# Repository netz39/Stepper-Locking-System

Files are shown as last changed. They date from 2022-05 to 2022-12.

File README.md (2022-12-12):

# Stepper Locking System

Steering the key/door knob with the might of stepper motors.
See the [Wiki](https://wiki.netz39.de/projects:2022:stepper_locking_system) (german) for more details and an overview.

This is forked from https://github.com/sprenger120/StepperServo.

## Firmware
The firmware written in C++ is [here](https://github.com/netz39/Stepper-Locking-System_firmware).

## Requirements for v1.0

* control stepper motor with Trinamic IC
* hall encoder connection to get current motor state
* read motor temperature
* CAN peripherie (dedicated PCB)
* power rails are secured by two fuses, with reverse polarity/overvoltage protection
* drive syncronous addressable LEDs
* get states from door and lock
* connection to two buttons to open/close door
* switch on/off Nerdstern (outdoor lamp)

## Known issues in v1.0
* Mosfet Q1 has wrong connections for choosen part. Gate and Source are swapped.
    * can be solved by simply solder the part upside down
* the LQFP32 package of STM32G0B1KE doesn't support HSE connection
    * the internal HSI is used

## Pictures (v1.0)

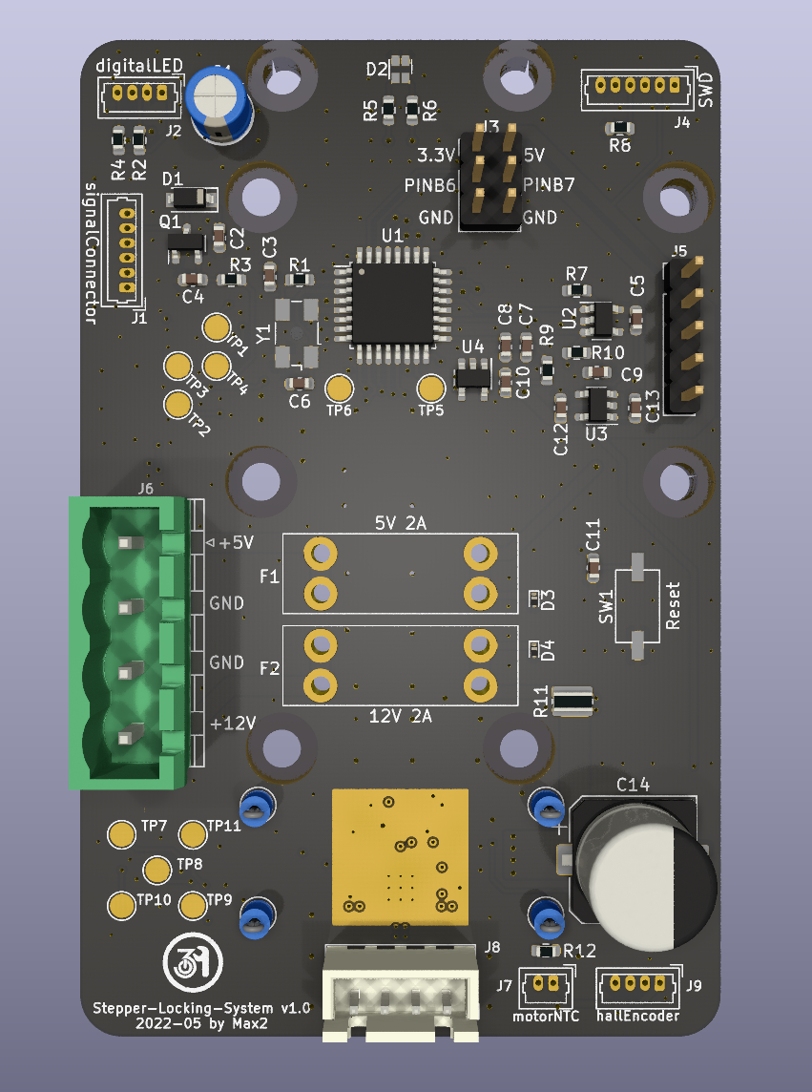
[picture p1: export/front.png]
pcb front front view


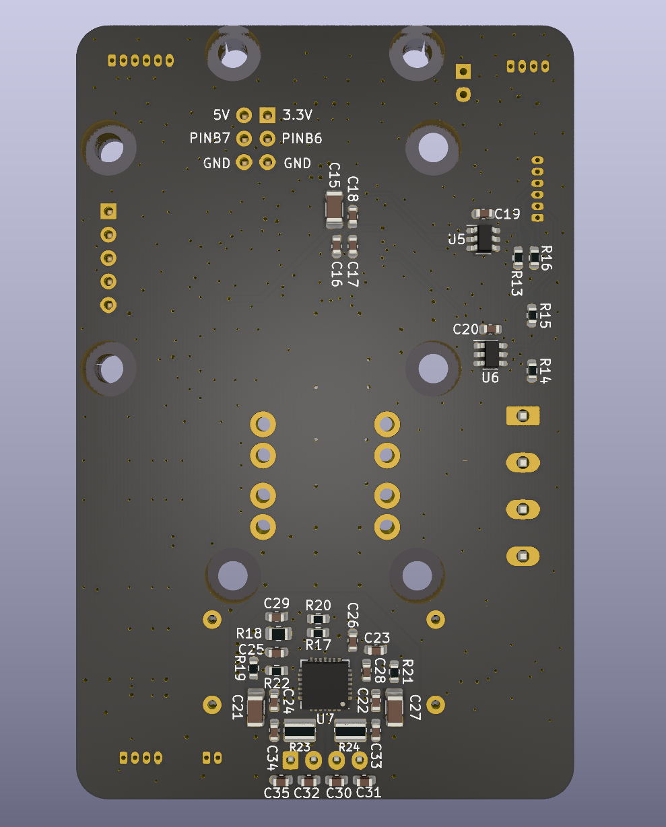
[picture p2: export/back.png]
pcb back back view


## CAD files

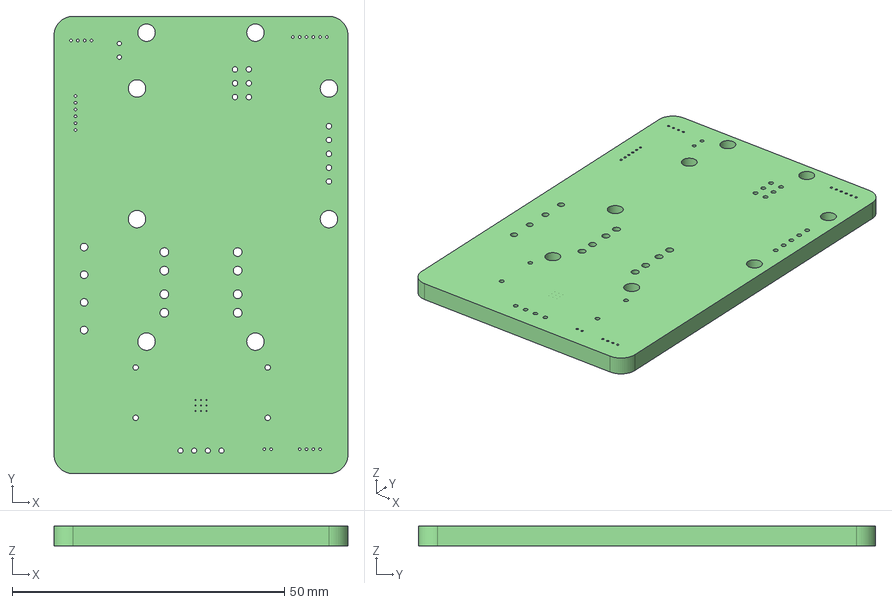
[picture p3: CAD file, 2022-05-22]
export/StepperLockingSystem.step
54.0 x 84.0 x 3.66 mm

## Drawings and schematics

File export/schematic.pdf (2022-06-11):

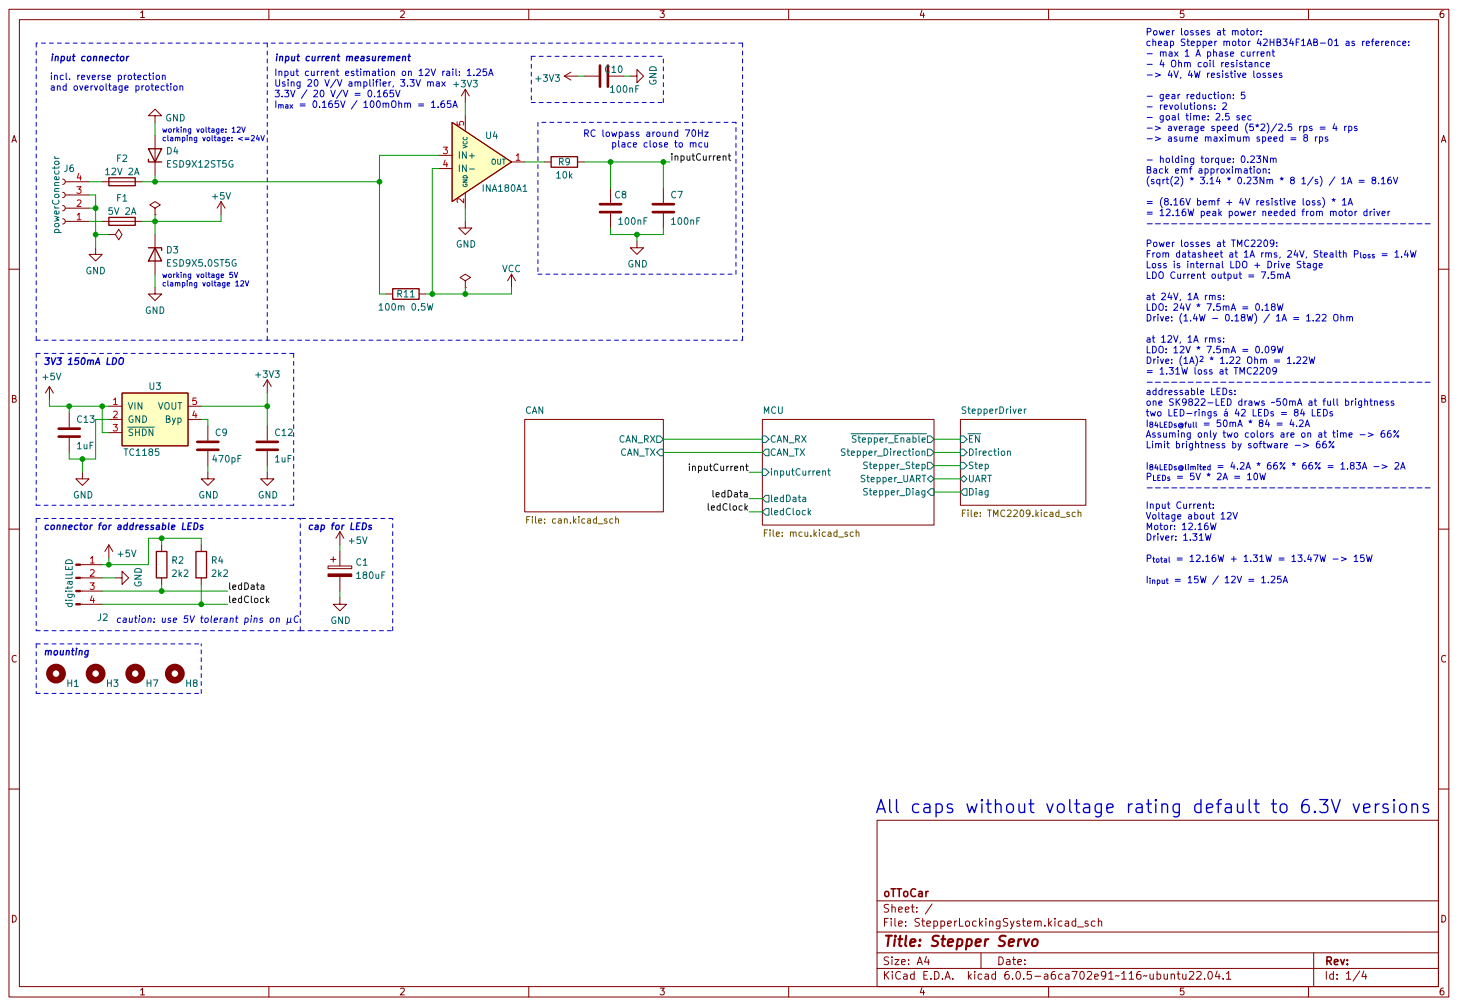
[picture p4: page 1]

- max 1 A phase current - 4 Ohm coil resistance

input current measurement 3V3 150mA LDO
incl. reverse protection
and overvoltage protection

Input current estimation on 12V rail: 1.25A
Using 20 V/V amplifier, 3.3V max 3.3V / 20 V/V = 0.165V

- gear reduction: 5
- revolutions: 2
- goal time: 2.5 sec
-> average speed (5*2)/2.5 rps = 4 rps
-> asume maximum speed = 8 rps

= (8.16V bemf + 4V resistive loss) * 1A
= 12.16W peak power needed from motor driver

----------------------------------- Power losses at TMC2209: From datasheet at 1A rms, 24V, Stealth P_{loss} = 1.4W

Loss is internal LDO + Drive Stage
LDO Current output = 7.5mA

Drive: (1A)^{2} * 1.22 Ohm = 1.22W
= 1.31W loss at TMC2209
addressable LEDs: one SK9822-LED draws ~50mA at full brightness

----------------------------------- All caps without voltage rating default to 6.3V versions
ledClock MCU

File: StepperLockingSystem.kicad_sch Sheet: / oTToCar CAN_RX CAN_TX CAN

I_{84LEDs@full} = 50mA * 84 = 4.2A
Assuming only two colors are on at time -> 66%
Limit brightness by software -> 66%

connector for addressable LEDs

Id: 1/4 Title: Stepper Servo

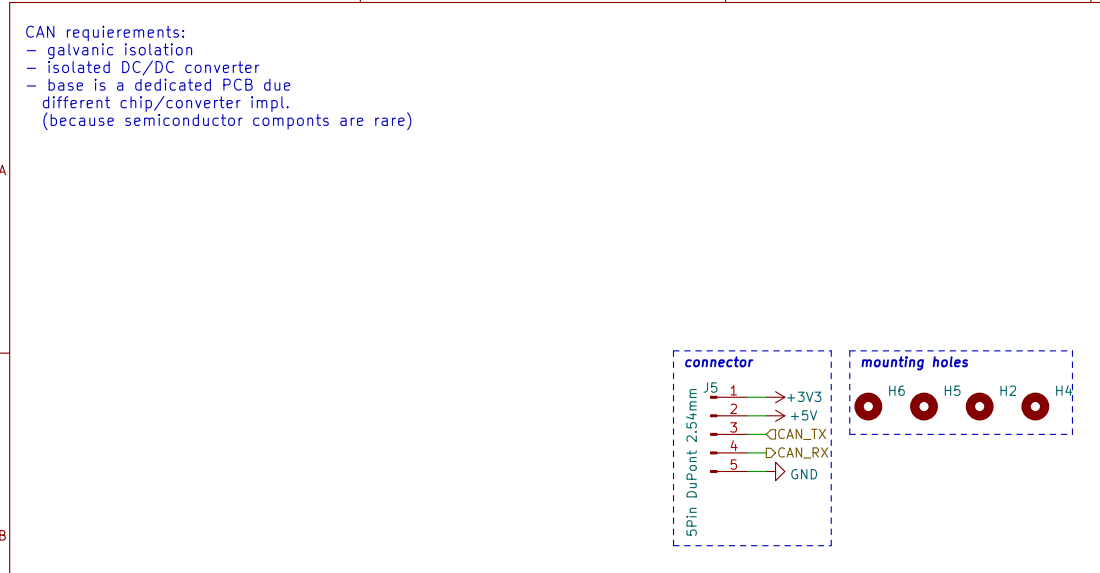
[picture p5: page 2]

CAN requierements:
- galvanic isolation
- isolated DC/DC converter
- base is a dedicated PCB due
different chip/converter impl.
(because semiconductor componts are rare)

File: can.kicad_sch Sheet: /CAN/
Id: 4/4 Title:

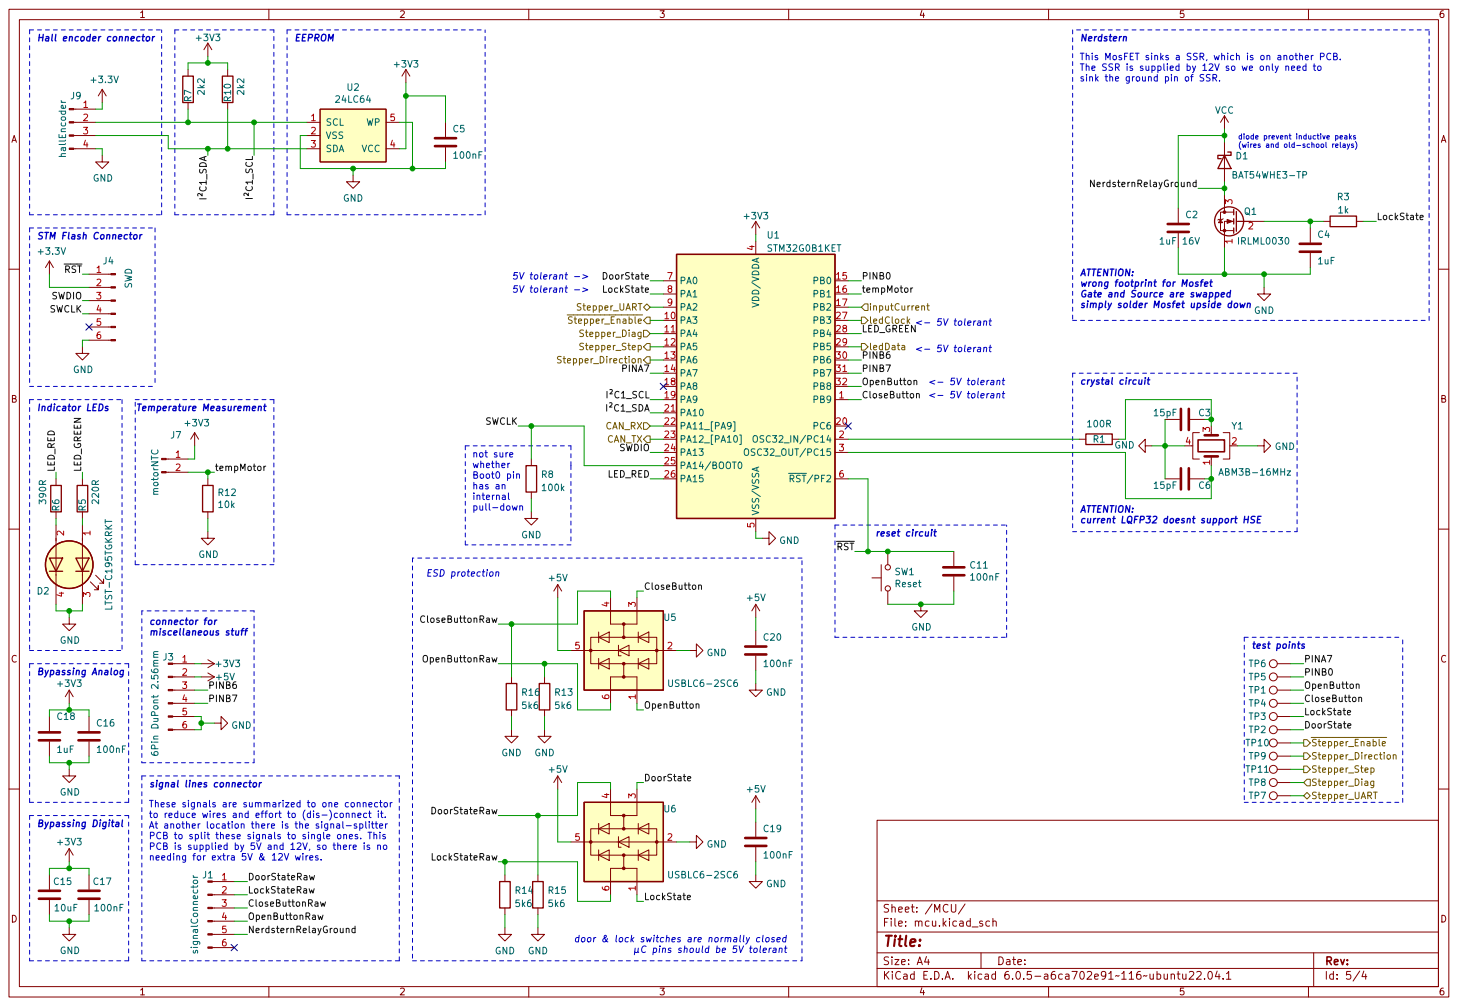
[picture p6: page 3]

Nerdstern
This MosFET sinks a SSR, which is on another PCB. The SSR is supplied by 12V so we only need to

(wires and old-school relays) not sure whether Boot0 pin

Gate and Source are swapped
simply solder Mosfet upside down

LockState CloseButton PINA7 PINA7 SWCLK DoorStateRaw

to reduce wires and effort to (dis-)connect it.
At another location there is the signal-splitter
PCB to split these signals to single ones. This
PCB is supplied by 5V and 12V, so there is no
needing for extra 5V & 12V wires.

File: mcu.kicad_sch Sheet: /MCU/
Id: 5/4 Title:

door & lock switches are normally closed

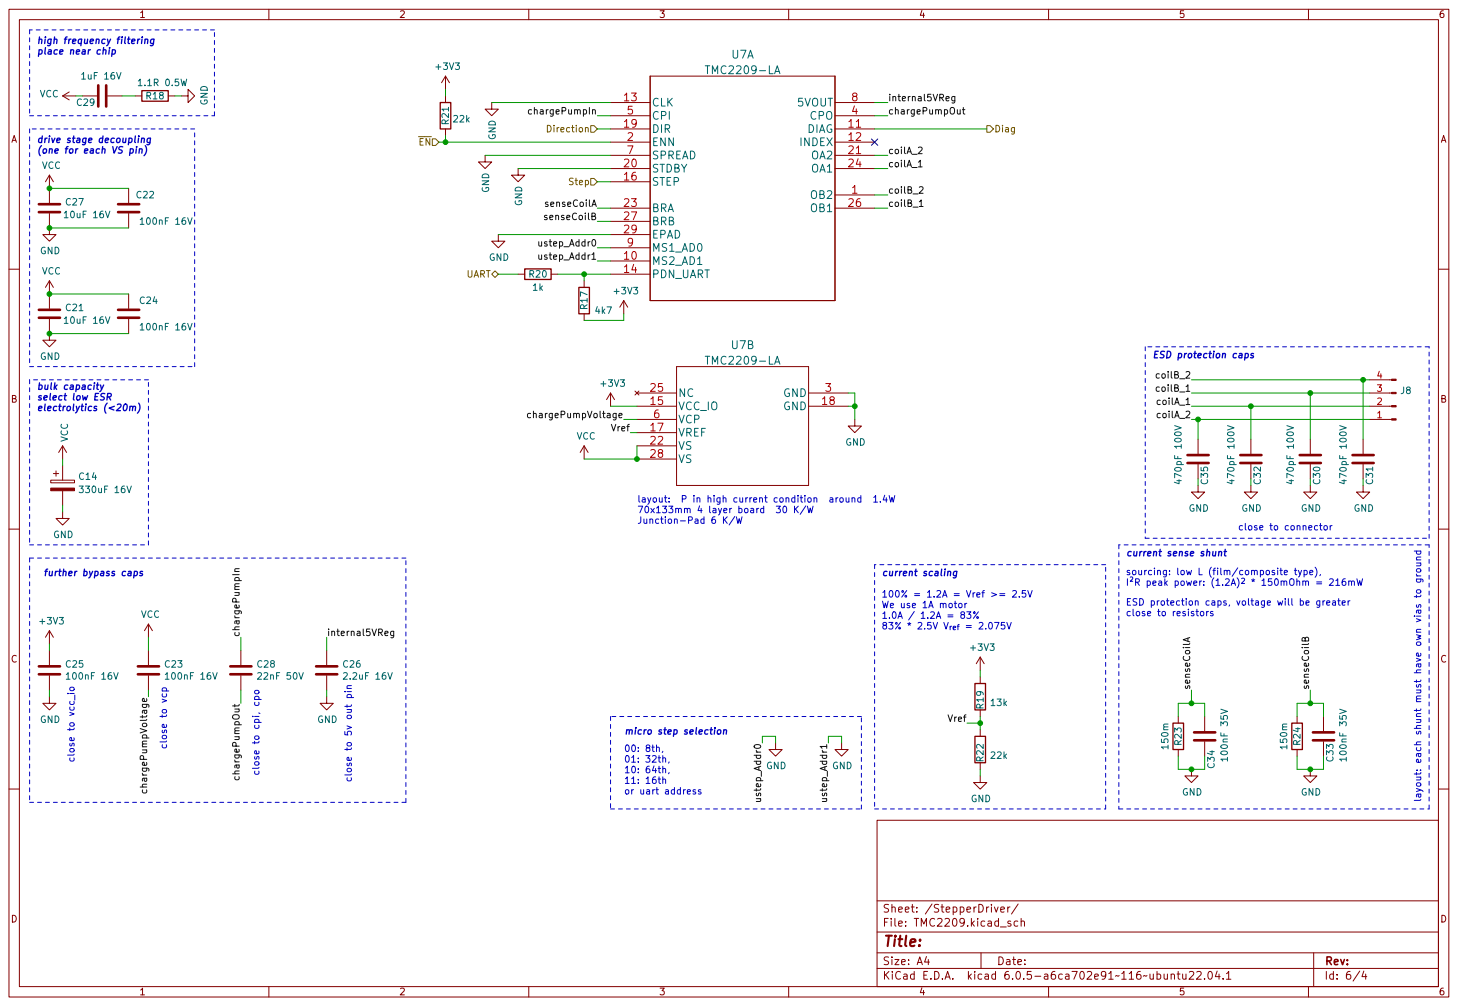
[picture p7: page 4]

Sheet: /StepperDriver/ GND VCC GND

layout: P in high current condition around 1.4W
70x133mm 4 layer board 30 K/W
Junction-Pad 6 K/W

current sense shunt close to 5v out pin

further bypass caps | 22nF 50V C23

current scaling 83% * 2.5V V_{ref} = 2.075V

sourcing: low L (film/composite type),

Vref 100% = 1.2A = Vref >= 2.5V We use 1A motor 1.0A / 1.2A = 83%

ESD protection caps, voltage will be greater close to resistors

or uart address micro step selection

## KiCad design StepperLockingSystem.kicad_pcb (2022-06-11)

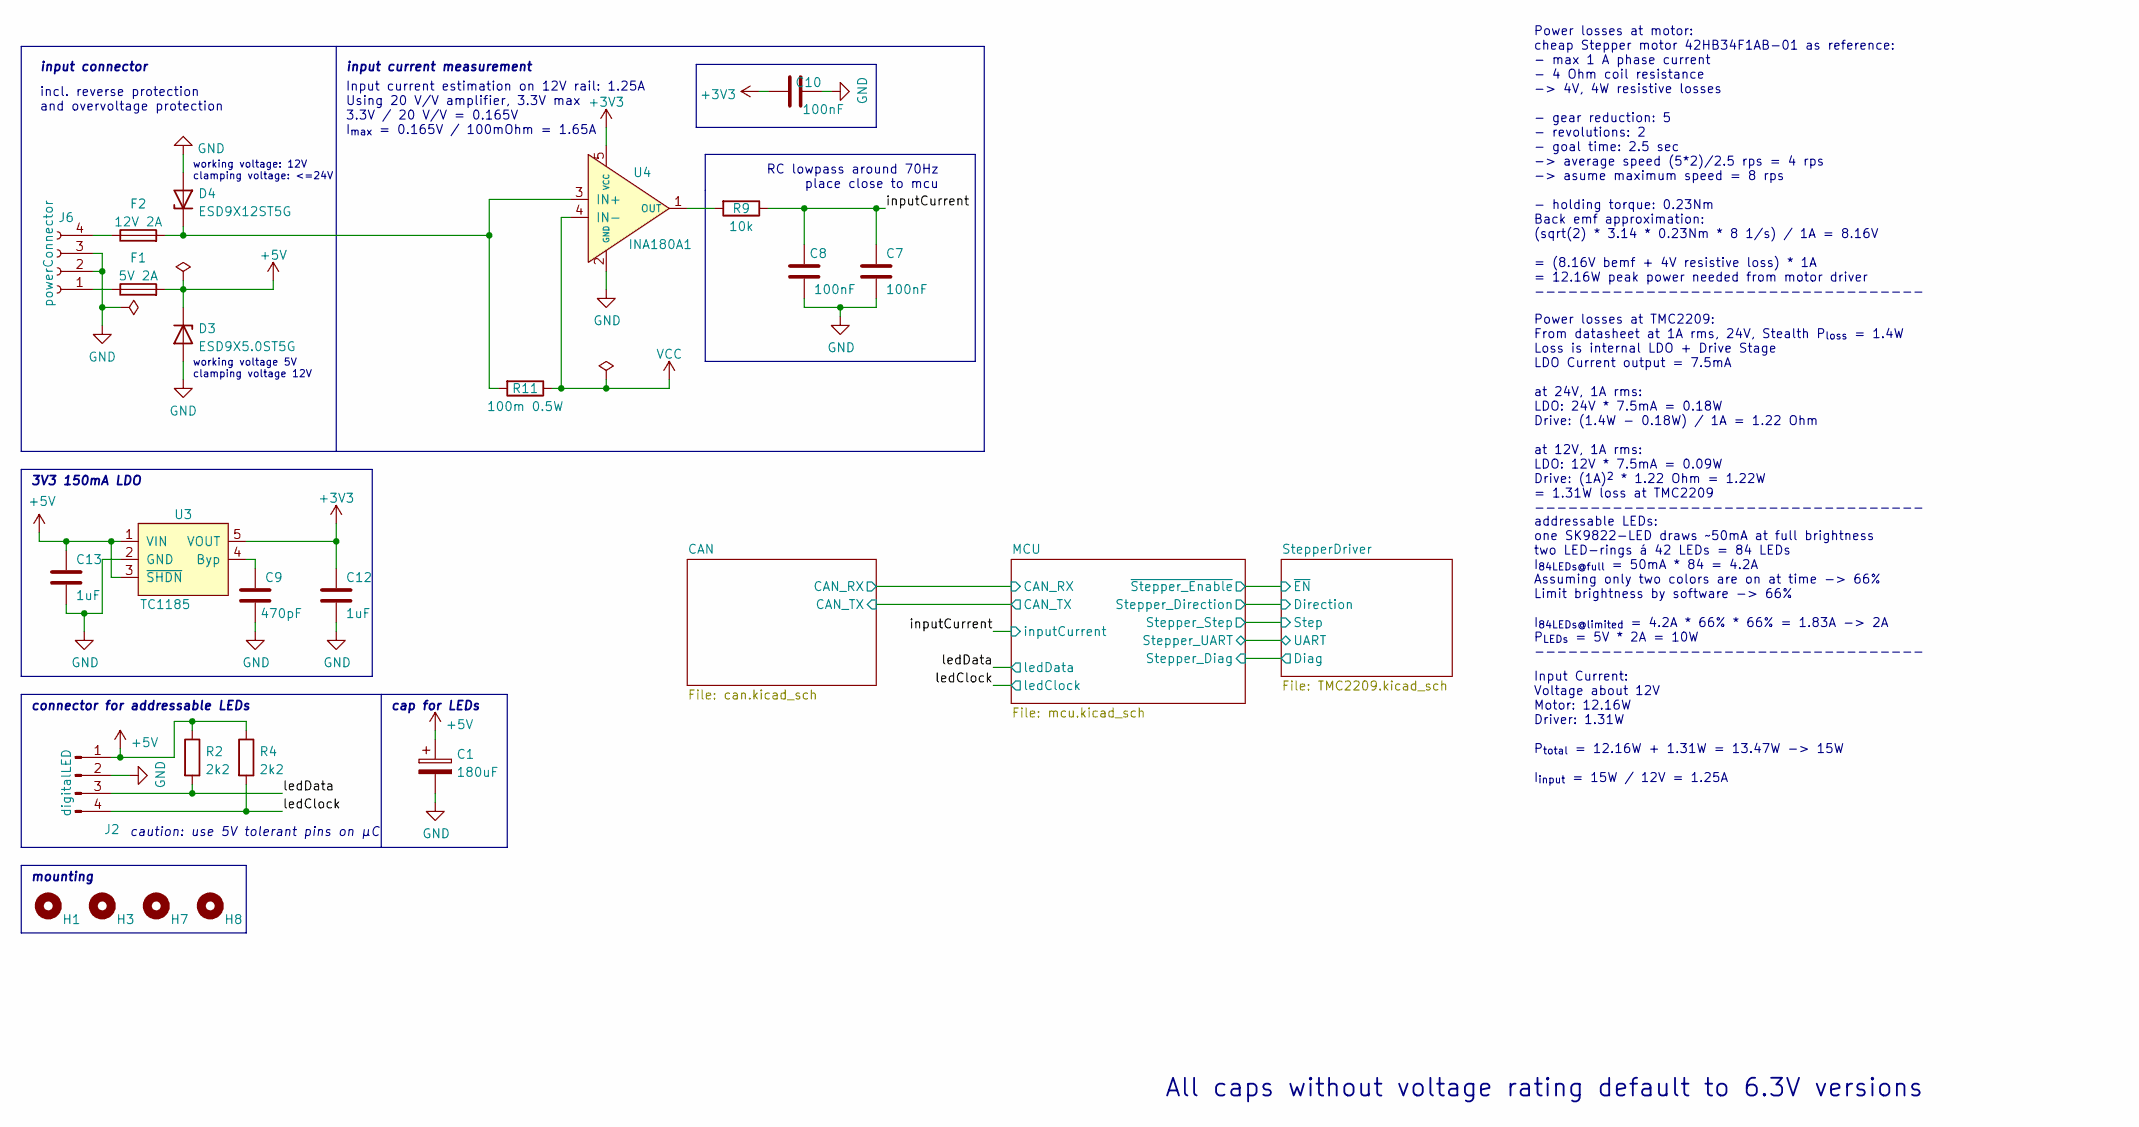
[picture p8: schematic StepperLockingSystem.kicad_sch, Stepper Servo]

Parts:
C1: 180uF; CP_Radial_D5.0mm_P2.50mm
C7, C8, C10: 100nF; C_0603_1608Metric
C9: 470pF; C_0603_1608Metric
C12, C13: 1uF; C_0603_1608Metric
D3: ESD9X5.0ST5G; D_SOD-923
D4: ESD9X12ST5G; D_SOD-923
F1: 5V 2A; KEYSTONE-FUSE-3557-2
F2: 12V 2A; KEYSTONE-FUSE-3557-2
H1, H3, H7, H8: MountingHole_Pad; MountingHole_3.2mm_M3_ISO7380_Keepout
J2: digitalLED; Molex_PicoBlade_53047-0410_1x04_P1.25mm_Vertical
J6: powerConnector; PhoenixContact_MSTBVA_2,5_4-G-5,08_1x04_P5.08mm_Vertical
R2, R4: 2k2; R_0603_1608Metric
R9: 10k; R_0603_1608Metric
R11: 100m 0.5W; R_0612_1632Metric
U3: TC1185; SOT-23-5
U4: INA180A1; SOT-23-5

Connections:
+5V: C1.1, C13.1, D3.1 (K), F1.2, J2.1, R2.1, R4.1, U3.1 (VIN), U3.3 (~SHDN); also elsewhere on the board
/inputCurrent: C7.1, C8.1, R9.1; also elsewhere on the board
/ledClock: J2.4, R4.2; also elsewhere on the board
/ledData: J2.3, R2.2; also elsewhere on the board
GND: C1.2, C7.2, C8.2, C9.2, C10.2, C12.2, C13.2, D3.2 (A), D4.2 (A), J2.2, J6.2, J6.3, U3.2 (GND), U4.2 (GND); also elsewhere on the board
unnamed: C9.1, U3.4 (Byp)
unnamed: D4.1 (K), F2.2, R11.2, U4.3 (IN+)
unnamed: F1.1, J6.1
unnamed: F2.1, J6.4
unnamed: R9.2, U4.1 (OUT)
VCC: R11.1, U4.4 (IN-); also elsewhere on the board

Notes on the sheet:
All caps without voltage rating default to 6.3V versions
caution: use 5V tolerant pins on µC
working voltage: 12V clamping voltage: <=24V
Input current estimation on 12V rail: 1.25A Using 20 V/V amplifier, 3.3V max 3.3V / 20 V/V = 0.165V I_{max} = 0.165V / 100mOhm = 1.65A
Power losses at TMC2209: From datasheet at 1A rms, 24V, Stealth P_{loss} = 1.4W Loss is internal LDO + Drive Stage LDO Current output = 7.5mA at 24V, 1A rms: LDO: 24V * 7.5mA = 0.18W Drive: (1.4W - 0.18W) / 1A = 1.22 Ohm at 12V, 1A rms: LDO: 12V * 7.5mA = 0.09W Drive: (1A)^{2} * 1.22 Ohm = 1.22W = 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
RC lowpass around 70Hz place close to mcu
working voltage 5V clamping voltage 12V
input connector
addressable LEDs: one SK9822-LED draws ~50mA at full brightness two LED-rings á 42 LEDs = 84 LEDs I_{84LEDs@full} = 50mA * 84 = 4.2A Assuming only two colors are on at time -> 66% Limit brightness by software -> 66% I_{84LEDs@limited} = 4.2A * 66% * 66% = 1.83A -> 2A P_{LEDs} = 5V * 2A = 10W ------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
3V3 150mA LDO
connector for addressable LEDs
input current measurement
cap for LEDs
incl. reverse protection and overvoltage protection
mounting
Input Current: Voltage about 12V Motor: 12.16W Driver: 1.31W P_{total} = 12.16W + 1.31W = 13.47W -> 15W I_{input} = 15W / 12V = 1.25A
Power losses at motor: cheap Stepper motor 42HB34F1AB-01 as reference: - max 1 A phase current - 4 Ohm coil resistance -> 4V, 4W resistive losses - gear reduction: 5 - revolutions: 2 - goal time: 2.5 sec -> average speed (5*2)/2.5 rps = 4 rps -> asume maximum speed = 8 rps - holding torque: 0.23Nm 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

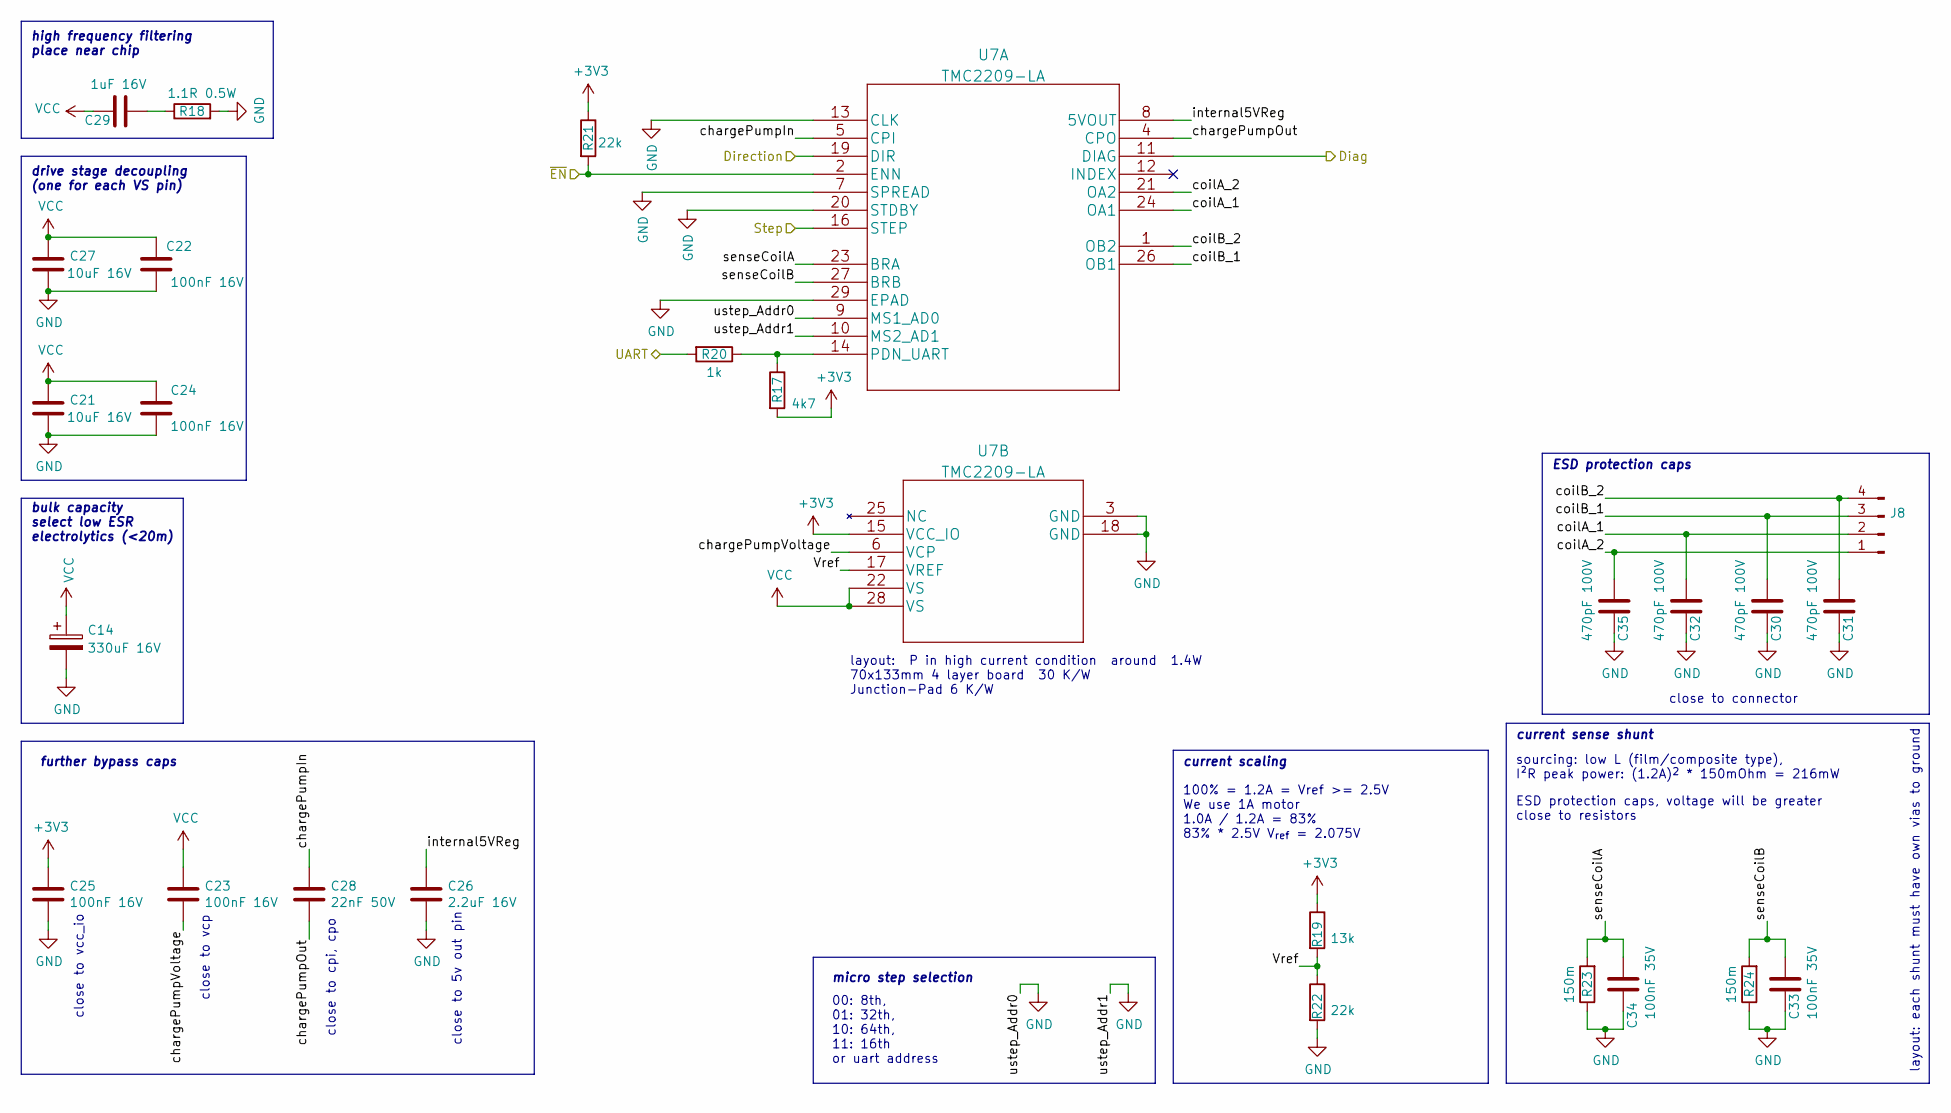
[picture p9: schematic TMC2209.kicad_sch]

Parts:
C14: 330uF 16V; CP_Elec_10x10.5
C21, C27: 10uF 16V; C_1206_3216Metric
C22, C23, C24, C25: 100nF 16V; C_0603_1608Metric
C26: 2.2uF 16V; C_0603_1608Metric
C28: 22nF 50V; C_0603_1608Metric
C29: 1uF 16V; C_0603_1608Metric
C30, C31, C32, C35: 470pF 100V; C_0603_1608Metric
C33, C34: 100nF 35V; C_0603_1608Metric
J8: Stepper; JST_XH_B4B-XH-A_1x04_P2.50mm_Vertical
R17: 4k7; R_0603_1608Metric
R18: 1.1R 0.5W; R_0805_2012Metric
R19: 13k; R_0603_1608Metric
R20: 1k; R_0603_1608Metric
R21, R22: 22k; R_0603_1608Metric
R23, R24: 150m; R_0612_1632Metric
U7: TMC2209-LA; QFN-28-1EP_5x5mm_P0.5mm_EP3.35x3.35mm_ThermalVias

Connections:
/MCU/Stepper_Diag: U7.11 (DIAG); also elsewhere on the board
/MCU/Stepper_Direction: U7.19 (DIR); also elsewhere on the board
/MCU/Stepper_Step: U7.16 (STEP); also elsewhere on the board
/MCU/Stepper_UART: R20.2; also elsewhere on the board
/MCU/~Stepper_Enable: R21.2, U7.2 (ENN); also elsewhere on the board
/StepperDriver/Vref: R19.2, R22.1, U7.17 (VREF)
/StepperDriver/chargePumpIn: C28.1, U7.5 (CPI)
/StepperDriver/chargePumpOut: C28.2, U7.4 (CPO)
/StepperDriver/chargePumpVoltage: C23.2, U7.6 (VCP)
/StepperDriver/coilA_1: C32.1, J8.2, U7.24 (OA1)
/StepperDriver/coilA_2: C35.1, J8.1, U7.21 (OA2)
/StepperDriver/coilB_1: C30.1, J8.3, U7.26 (OB1)
/StepperDriver/coilB_2: C31.1, J8.4, U7.1 (OB2)
/StepperDriver/internal5VReg: C26.1, U7.8 (5VOUT)
/StepperDriver/senseCoilA: C34.1, R23.2, U7.23 (BRA)
/StepperDriver/senseCoilB: C33.1, R24.2, U7.27 (BRB)
GND: C14.2, C21.2, C22.2, C24.2, C25.2, C26.2, C27.2, C30.2, C31.2, C32.2, C33.2, C34.2, C35.2, R18.2, R22.2, R23.1, R24.1, U7.3 (GND), U7.7 (SPREAD), U7.9 (MS1_AD0), U7.10 (MS2_AD1), U7.13 (CLK), U7.18 (GND), U7.20 (STDBY), U7.29 (EPAD); also elsewhere on the board
unnamed: C29.2, R18.1
unnamed: R17.1, R20.1, U7.14 (PDN_UART)
VCC: C14.1, C21.1, C22.1, C23.1, C24.1, C27.1, C29.1, U7.22 (VS), U7.28 (VS); also elsewhere on the board

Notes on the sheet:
layout: each shunt must have own vias to ground
100% = 1.2A = Vref >= 2.5V We use 1A motor 1.0A / 1.2A = 83% 83% * 2.5V V_{ref} = 2.075V
close to connector
close to vcc_io
bulk capacity select low ESR electrolytics (<20m)
drive stage decoupling (one for each VS pin)
current scaling
further bypass caps
micro step selection
ESD protection caps, voltage will be greater close to resistors
sourcing: low L (film/composite type), I²R peak power: (1.2A)^{2} * 150mOhm = 216mW
close to vcp
current sense shunt
close to cpi, cpo
00: 8th, 01: 32th, 10: 64th, 11: 16th or uart address
ESD protection caps
layout: P in high current condition around 1.4W 70x133mm 4 layer board 30 K/W Junction-Pad 6 K/W
high frequency filtering place near chip
close to 5v out pin

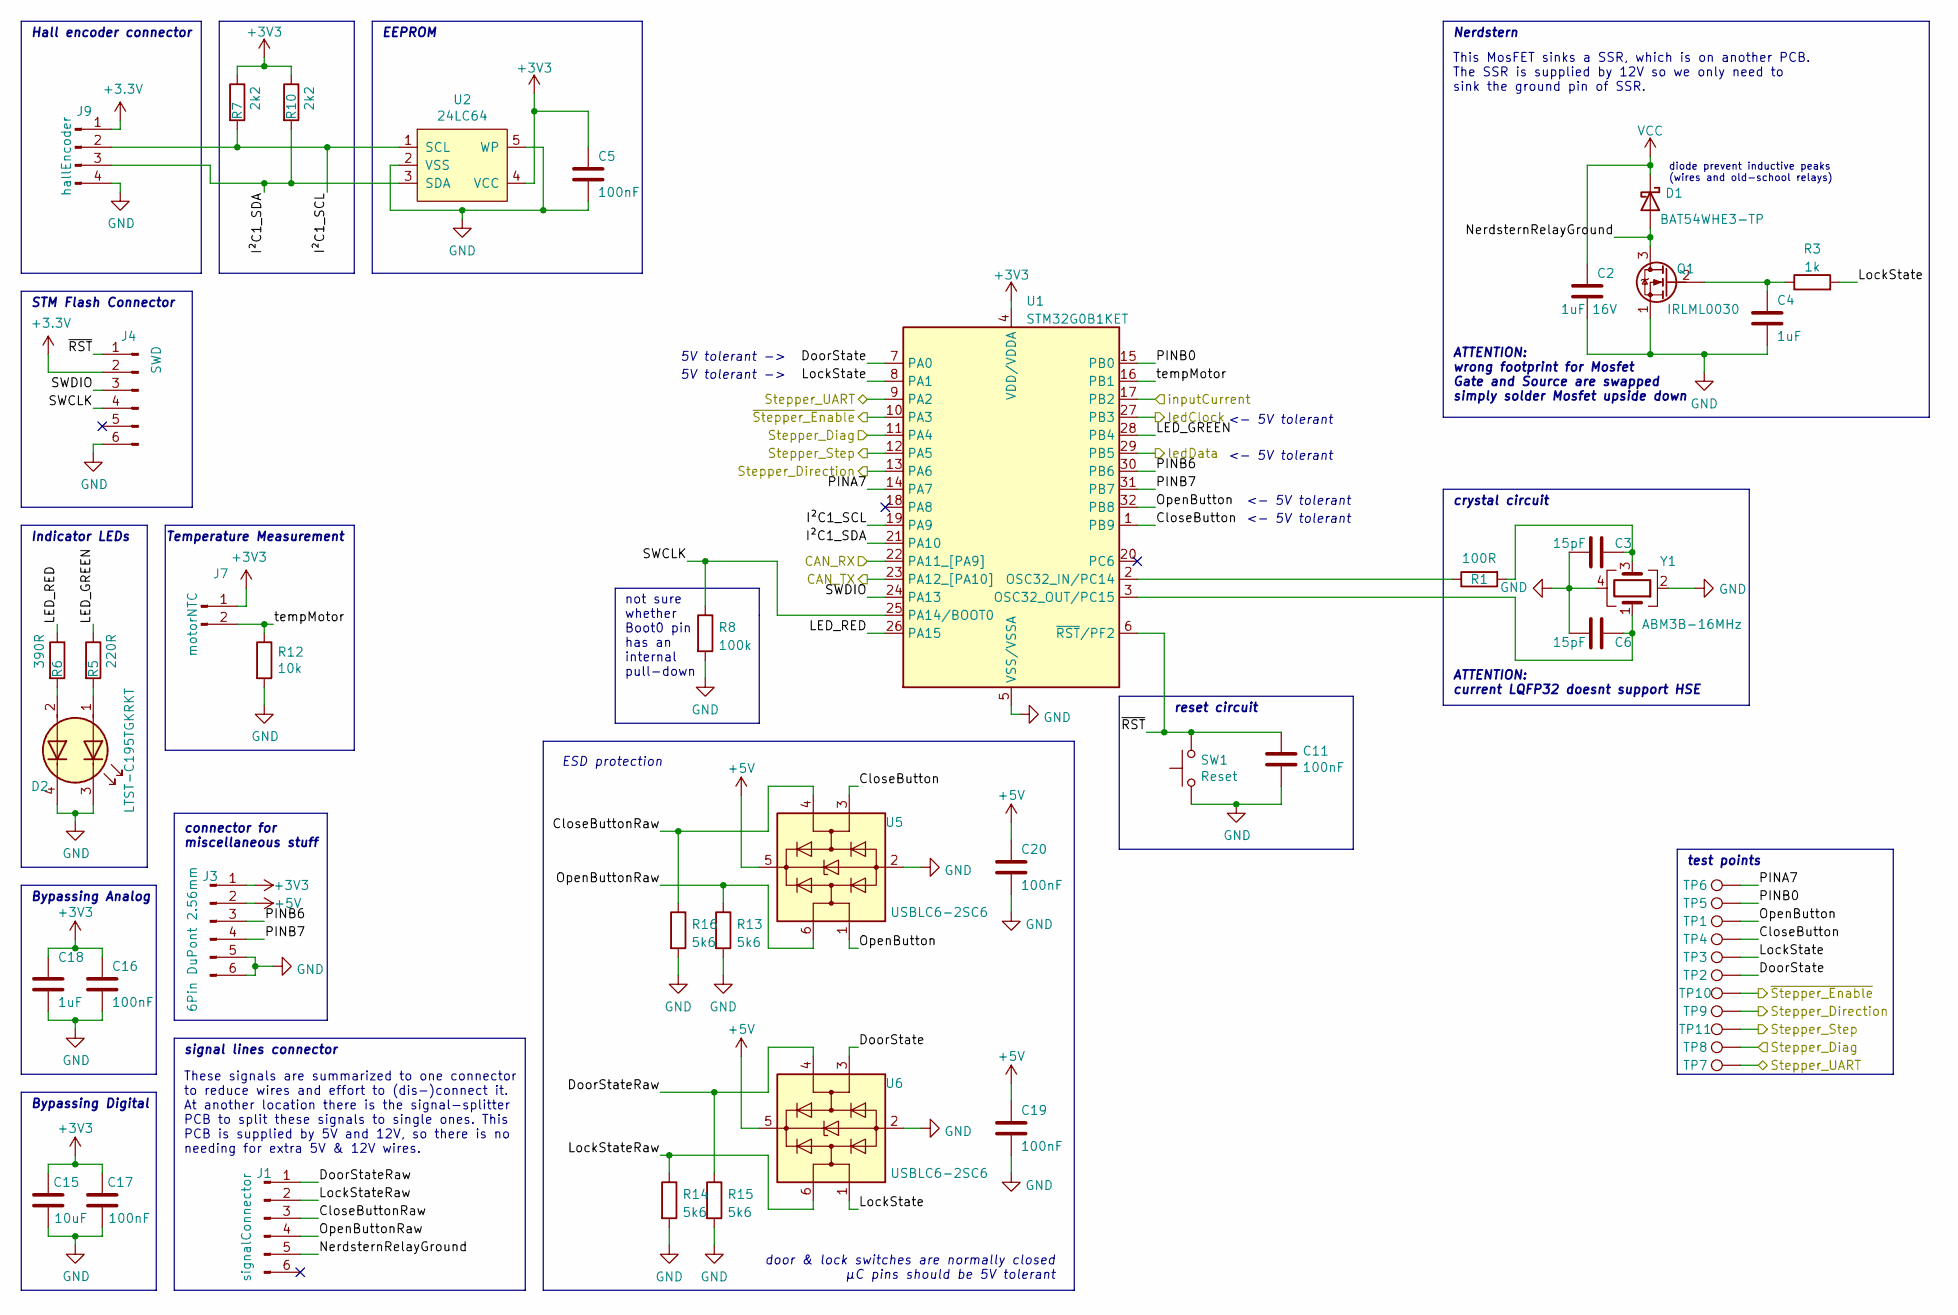
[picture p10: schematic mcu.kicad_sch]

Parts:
C2: 1uF 16V; C_0603_1608Metric
C3, C6: 15pF; C_0603_1608Metric
C4, C18: 1uF; C_0603_1608Metric
C5, C11, C16, C17, C19, C20: 100nF; C_0603_1608Metric
C15: 10uF; C_1206_3216Metric
D1: BAT54WHE3-TP; D_SOD-123
D2: LTST-C195TGKRKT; LED_LiteOn_LTST-C195TGKRKT
J1: signalConnector; Molex_PicoBlade_53047-0610_1x06_P1.25mm_Vertical
J3: 6Pin DuPont 2.56mm; PinHeader_2x03_P2.54mm_Vertical
J4: SWD; Molex_PicoBlade_53047-0610_1x06_P1.25mm_Vertical
J7: motorNTC; Molex_PicoBlade_53047-0210_1x02_P1.25mm_Vertical
J9: hallEncoder; Molex_PicoBlade_53047-0410_1x04_P1.25mm_Vertical
Q1: IRLML0030; SOT-23
R1: 100R; R_0603_1608Metric
R3: 1k; R_0603_1608Metric
R5: 220R; R_0603_1608Metric
R6: 390R; R_0603_1608Metric
R7, R10: 2k2; R_0603_1608Metric
R8: 100k; R_0603_1608Metric
R12: 10k; R_0603_1608Metric
R13, R14, R15, R16: 5k6; R_0603_1608Metric
SW1: Reset; PTS636_F-leads
TP1, TP2, TP3, TP4, TP5, TP6, TP7, TP8, TP9, TP10, TP11: TestPoint; TestPoint_Pad_D2.0mm
U1: STM32G0B1KET; LQFP-32_7x7mm_P0.8mm
U2: 24LC64; SOT-23-5
U5, U6: USBLC6-2SC6; SOT-23-6
Y1: ABM3B-16MHz; Crystal_SMD_Abracon_ABM3B-4Pin_5.0x3.2mm

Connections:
+5V: C19.2, C20.2, J3.2, U5.5 (VBUS), U6.5 (VBUS); also elsewhere on the board
/CAN/CAN_RX: U1.22 (PA11_[PA9]); also elsewhere on the board
/CAN/CAN_TX: U1.23 (PA12_[PA10]); also elsewhere on the board
/MCU/CloseButton: TP4.1, U1.1 (PB9), U5.3 (I/O2)
/MCU/CloseButtonRaw: J1.3, R16.1, U5.4 (I/O2)
/MCU/DoorState: TP2.1, U1.7 (PA0), U6.3 (I/O2)
/MCU/DoorStateRaw: J1.1, R15.1, U6.4 (I/O2)
/MCU/I²C1_SCL: J9.2, R7.2, U1.19 (PA9), U2.1 (SCL)
/MCU/I²C1_SDA: J9.3, R10.2, U1.21 (PA10), U2.3 (SDA)
/MCU/LED_GREEN: R5.1, U1.28 (PB4)
/MCU/LED_RED: R6.1, U1.26 (PA15)
/MCU/LockState: R3.2, TP3.1, U1.8 (PA1), U6.1 (I/O1)
/MCU/LockStateRaw: J1.2, R14.1, U6.6 (I/O1)
/MCU/NerdsternRelayGround: D1.2 (A), J1.5, Q1.3 (D)
/MCU/OpenButton: TP1.1, U1.32 (PB8), U5.1 (I/O1)
/MCU/OpenButtonRaw: J1.4, R13.1, U5.6 (I/O1)
/MCU/PINA7: TP6.1, U1.14 (PA7)
/MCU/PINB0: TP5.1, U1.15 (PB0)
/MCU/PINB6: J3.3, U1.30 (PB6)
/MCU/PINB7: J3.4, U1.31 (PB7)
/MCU/SWCLK: J4.4, R8.1, U1.25 (PA14/BOOT0)
/MCU/SWDIO: J4.3, U1.24 (PA13)
/MCU/Stepper_Diag: TP8.1, U1.11 (PA4); also elsewhere on the board
/MCU/Stepper_Direction: TP9.1, U1.13 (PA6); also elsewhere on the board
/MCU/Stepper_Step: TP11.1, U1.12 (PA5); also elsewhere on the board
/MCU/Stepper_UART: TP7.1, U1.9 (PA2); also elsewhere on the board
/MCU/tempMotor: J7.2, R12.1, U1.16 (PB1)
/MCU/~RST: C11.1, J4.1, SW1.2, U1.6 (~RST/PF2)
/MCU/~Stepper_Enable: TP10.1, U1.10 (PA3); also elsewhere on the board
/inputCurrent: U1.17 (PB2); also elsewhere on the board
/ledClock: U1.27 (PB3); also elsewhere on the board
/ledData: U1.29 (PB5); also elsewhere on the board
GND: C2.2, C3.1, C4.2, C5.2, C6.1, C11.2, C15.1, C16.2, C17.1, C18.2, C19.1, C20.1, D2.3 (K1), D2.4 (K2), J3.5, J3.6, J4.6, J9.4, Q1.1 (S), R8.2, R12.2, R13.2, R14.2, R15.2, R16.2, SW1.1, U1.5 (VSS/VSSA), U2.2 (VSS), U2.5 (WP), U5.2 (GND), U6.2 (GND), Y1.2, Y1.4; also elsewhere on the board
unnamed: C3.2, R1.2, Y1.3
unnamed: C4.1, Q1.2 (G), R3.1
unnamed: C6.2, U1.3 (OSC32_OUT/PC15), Y1.1
unnamed: D2.1 (A1), R5.2
unnamed: D2.2 (A2), R6.2
unnamed: R1.1, U1.2 (OSC32_IN/PC14)
VCC: C2.1, D1.1 (K); also elsewhere on the board

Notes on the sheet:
ATTENTION: wrong footprint for Mosfet Gate and Source are swapped simply solder Mosfet upside down
5V tolerant ->
crystal circuit
Bypassing Digital
Nerdstern
Bypassing Analog
reset circuit
not sure whether Boot0 pin has an internal pull-down
diode prevent inductive peaks (wires and old-school relays)
test points
<- 5V tolerant
ESD protection
Indicator LEDs
Hall encoder connector
door & lock switches are normally closed µC pins should be 5V tolerant
connector for miscellaneous stuff
ATTENTION: current LQFP32 doesnt support HSE
This MosFET sinks a SSR, which is on another PCB. The SSR is supplied by 12V so we only need to sink the ground pin of SSR.
EEPROM
These signals are summarized to one connector to reduce wires and effort to (dis-)connect it. At another location there is the signal-splitter PCB to split these signals to single ones. This PCB is supplied by 5V and 12V, so there is no needing for extra 5V & 12V wires.
Temperature Measurement
STM Flash Connector
signal lines connector

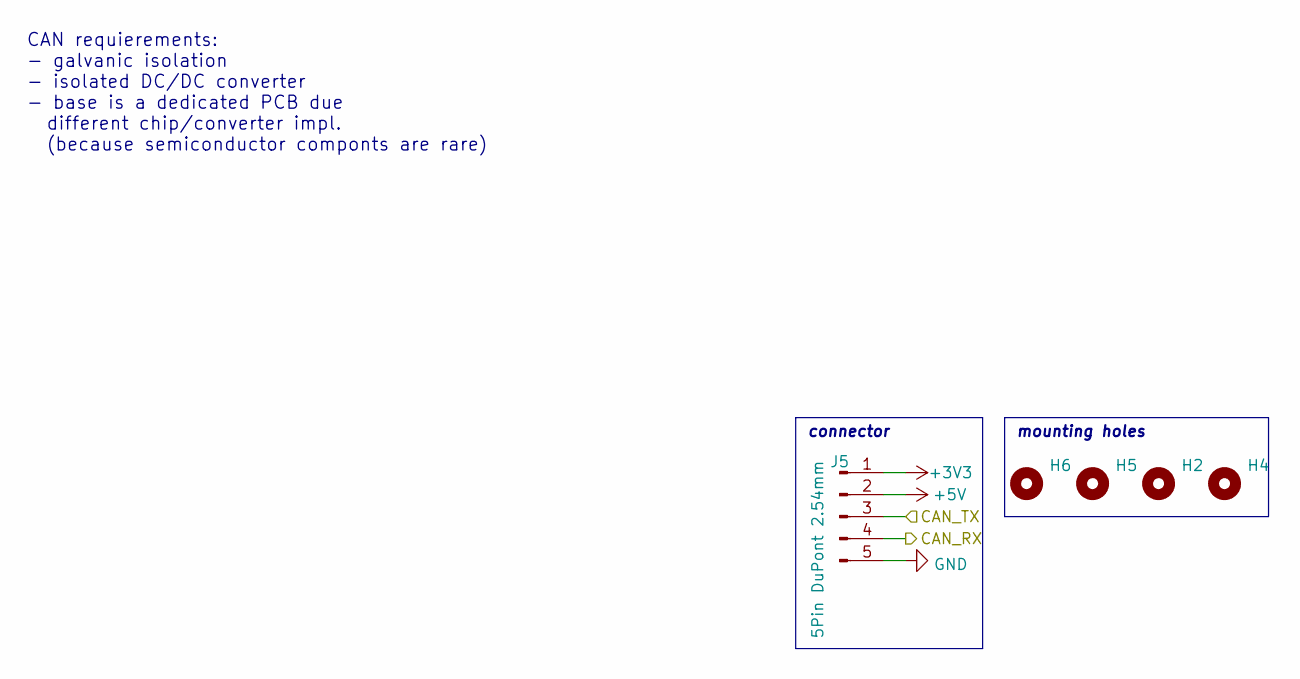
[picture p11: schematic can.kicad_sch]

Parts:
H2, H4, H5, H6: MountingHole_Pad; MountingHole_3.2mm_M3_ISO7380_Keepout
J5: 5Pin DuPont 2.54mm; PinHeader_1x05_P2.54mm_Vertical

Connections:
+5V: J5.2; also elsewhere on the board
/CAN/CAN_RX: J5.4; also elsewhere on the board
/CAN/CAN_TX: J5.3; also elsewhere on the board
GND: J5.5; also elsewhere on the board

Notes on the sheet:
mounting holes
CAN requierements: - galvanic isolation - isolated DC/DC converter - base is a dedicated PCB due different chip/converter impl. (because semiconductor componts are rare)
connector

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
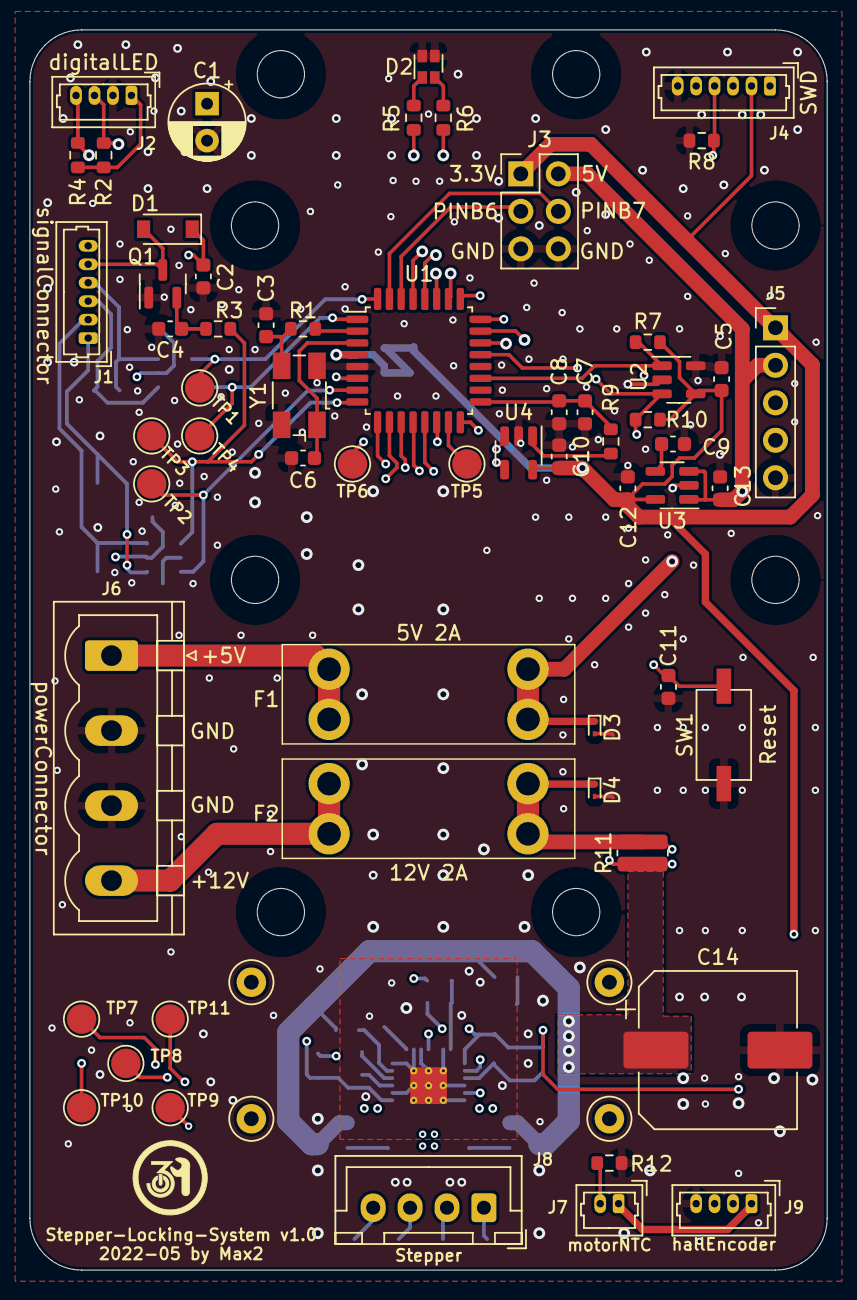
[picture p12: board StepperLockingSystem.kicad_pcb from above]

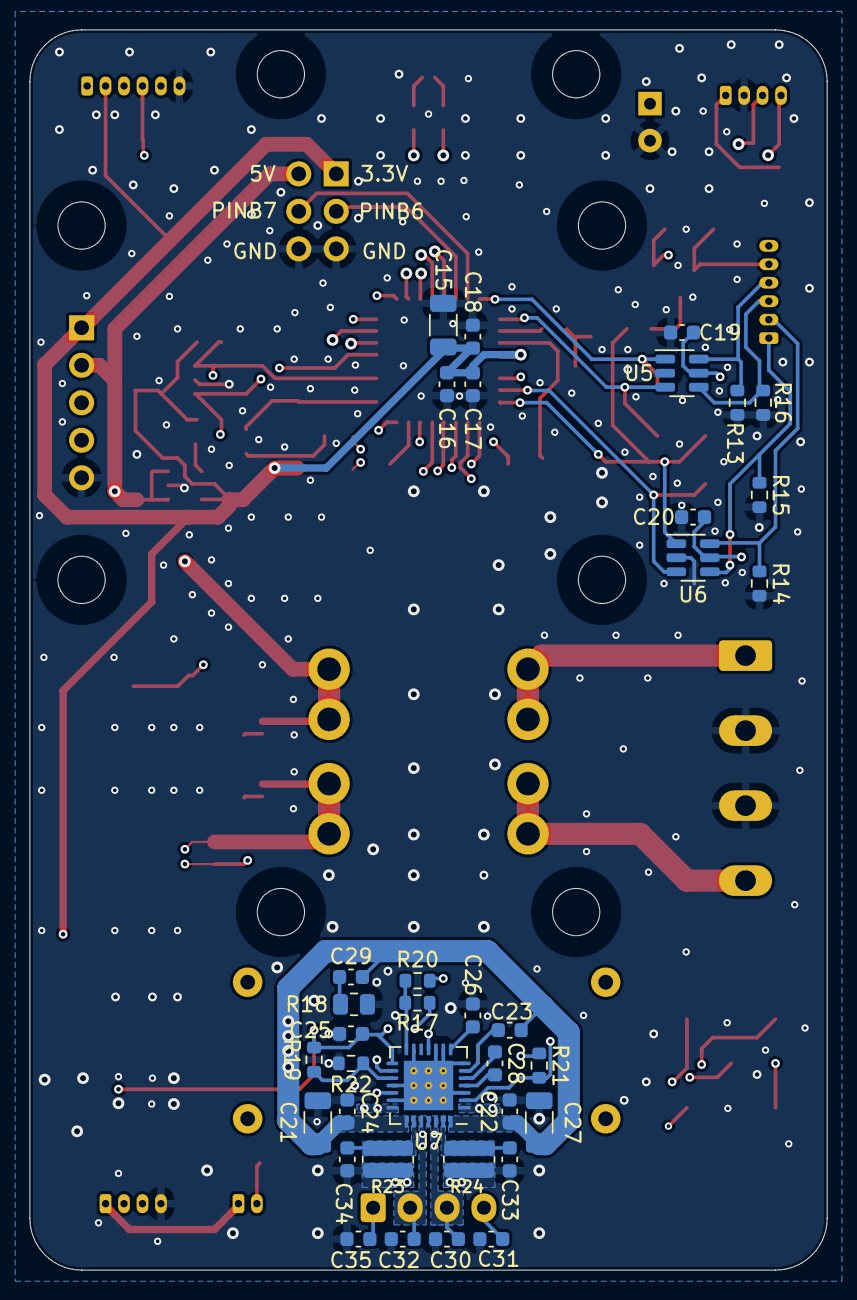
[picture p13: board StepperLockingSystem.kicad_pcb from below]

Board: 4 copper layers, 54.0 x 84.0 mm, 103 parts (36 on the bottom side), 59 nets.

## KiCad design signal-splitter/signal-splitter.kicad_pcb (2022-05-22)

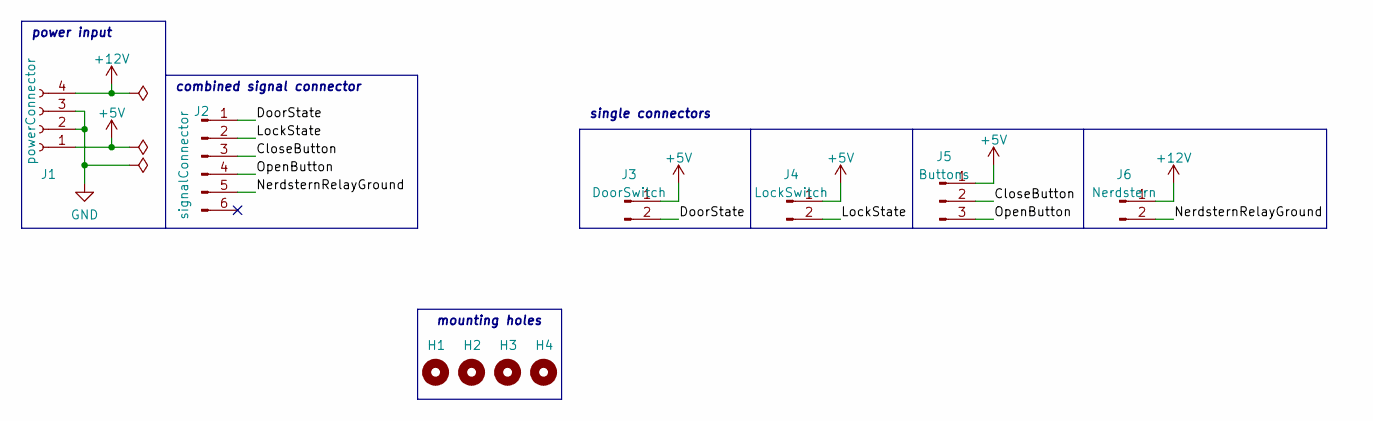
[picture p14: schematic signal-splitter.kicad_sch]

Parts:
H1, H2, H3, H4: MountingHole; MountingHole_3.2mm_M3_ISO14580
J1: powerConnector; PhoenixContact_MSTBA_2,5_4-G-5,08_1x04_P5.08mm_Horizontal
J2: signalConnector; Molex_PicoBlade_53047-0610_1x06_P1.25mm_Vertical
J3: DoorSwitch; Molex_PicoBlade_53047-0210_1x02_P1.25mm_Vertical
J4: LockSwitch; Molex_PicoBlade_53047-0210_1x02_P1.25mm_Vertical
J5: Buttons; Molex_PicoBlade_53047-0310_1x03_P1.25mm_Vertical
J6: Nerdstern; Molex_PicoBlade_53047-0210_1x02_P1.25mm_Vertical

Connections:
+5V: J1.1, J3.1, J4.1, J5.1
+12V: J1.4, J6.1
/CloseButton: J2.3, J5.2
/DoorState: J2.1, J3.2
/LockState: J2.2, J4.2
/NerdsternRelayGround: J2.5, J6.2
/OpenButton: J2.4, J5.3
GND: J1.2, J1.3

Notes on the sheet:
power input
single connectors
mounting holes
combined signal connector

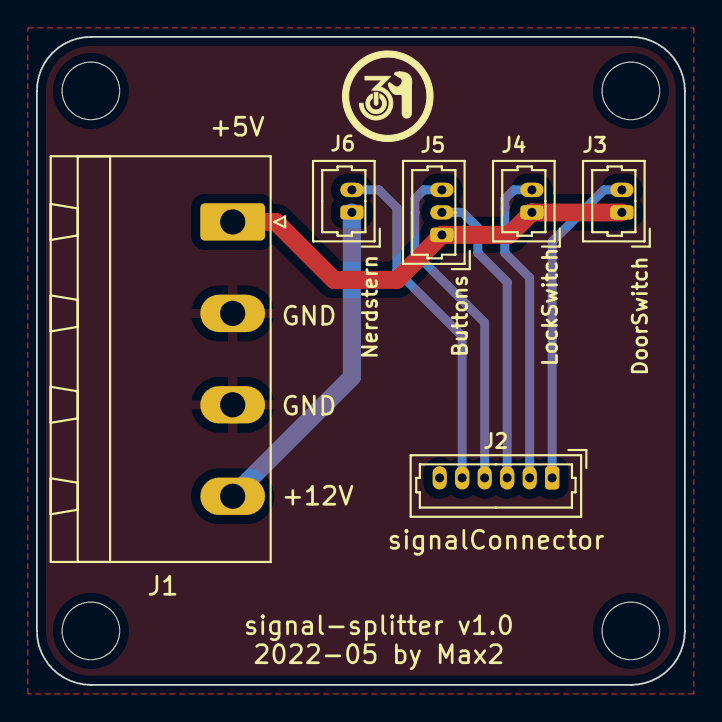
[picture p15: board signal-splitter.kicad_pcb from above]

Board: 2 copper layers, 36.0 x 36.0 mm, 10 parts (0 on the bottom side), 8 nets.

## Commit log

2022-01-12 Clean up
    [StepperServo-B_Cu.gbr, StepperServo-B_Mask.gbr, StepperServo-B_Paste.gbr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]
2022-01-12 Update to KiCad 6.0.0
    [Encoder.kicad_sch, Encoder.sch, ExternalEncoder.kicad_sch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]
2022-02-21 KiCad 6 changes
    [Encoder.kicad_sch, ExternalEncoder.kicad_sch, OpticalEndstop.kicad_sch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]
2022-02-21 Update notes
    [StepperServo.kicad_sch]
2022-04-04 Rename files Remove unnecessary contents
    [ExternalEncoder.kicad_sch, OpticalEndstop.kicad_sch, StepperLockingSystem.kicad_pcb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]
2022-04-04 Cleanup CAD, Datasheets and BOM
    [fp_omron sx3340 - Sketch 1.dxf, nema14 stepper - demo&pcb sketch.dxf]
2022-04-04 Rename footprint folder
2022-04-04 Rearrange schematic and some cleanups Add 5V buck converter Update values for TMC2209 Add EEPROM Switch to STM32G0B1KE
    [Encoder.kicad_sch, StepperLockingSystem.kicad_sch, TMC2209.kicad_sch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]
2022-04-04 Small changes
    [StepperLockingSystem.kicad_sch, TMC2209.kicad_sch, mcu.kicad_sch]
2022-04-07 Annotate symbols and assign footprints
    [StepperLockingSystem.kicad_sch, TMC2209.kicad_sch, buck.kicad_sch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]
2022-04-09 [WIP] Create PCB
    [StepperLockingSystem.kicad_pcb]
2022-05-10 Finish schematic
    [StepperLockingSystem.kicad_pcb, StepperLockingSystem.kicad_sch, TMC2209.kicad_sch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]
2022-05-12 Add many changes to schematic and WIP PCB
    [StepperLockingSystem.kicad_pcb, StepperLockingSystem.kicad_sch, TMC2209.kicad_sch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]
2022-05-12 Some changes to schematic
    [StepperLockingSystem.kicad_pcb, StepperLockingSystem.kicad_sch, TMC2209.kicad_sch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]
2022-05-15 Finish PCB layout
    [StepperLockingSystem.kicad_pcb, StepperLockingSystem.kicad_sch, TMC2209.kicad_sch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]
2022-05-15 Add ground plane vias
    [StepperLockingSystem.kicad_pcb]
2022-05-16 Add BOM and update some values due component order
    [StepperLockingSystem.kicad_pcb, StepperLockingSystem.kicad_sch, TMC2209.kicad_sch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]
2022-05-16 Update footprint and export step file
    [StepperLockingSystem.kicad_pcb, StepperLockingSystem.step]
2022-05-17 Change positions of mounting holes to middle
    [StepperLockingSystem.kicad_pcb, StepperLockingSystem.kicad_sch, StepperLockingSystem.step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]
2022-05-18 Add holes for heat sink
    [StepperLockingSystem.kicad_pcb]
2022-05-18 Move note
    [StepperLockingSystem.kicad_sch, TMC2209.kicad_sch]
2022-05-19 Add note to door/lock state switches
    [mcu.kicad_sch]
2022-05-22 Apply suggestions from tux: Single connector for signals Some (better) notes
    [StepperLockingSystem.kicad_pcb, StepperLockingSystem.kicad_sch, TMC2209.kicad_sch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]
2022-05-22 Change power input pin out Update exported stuffs Update ReadMe
    [StepperLockingSystem.kicad_pcb, StepperLockingSystem.kicad_sch, StepperLockingSystem.step]
2022-05-22 Add signal-splitter pcb
    [mcu.kicad_sch, signal-splitter.kicad_pcb, signal-splitter.kicad_sch]
2022-05-22 Add settings for Gerber
    [StepperLockingSystem.kicad_pcb, signal-splitter.kicad_pcb]
2022-06-11 Note two known issues
    [StepperLockingSystem.kicad_pcb, mcu.kicad_sch]
